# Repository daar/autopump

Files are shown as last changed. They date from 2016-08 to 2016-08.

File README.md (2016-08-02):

Autopump is a small project to create an Arduino powered automatic compressed air controller. The controller has an LCD screen and two button interface. Two automatic valves and a pressure transmitter make it possible to achieve accurate control on the target pressure. The original purpose to build such a controller was to make it possible to automatically pump soccer balls, although the controller of course can be used for any purpose.

Below is a rendering of the Arduino UNO shield that is needed to control autopump. The shield connects all peripherals to the Arduino board.

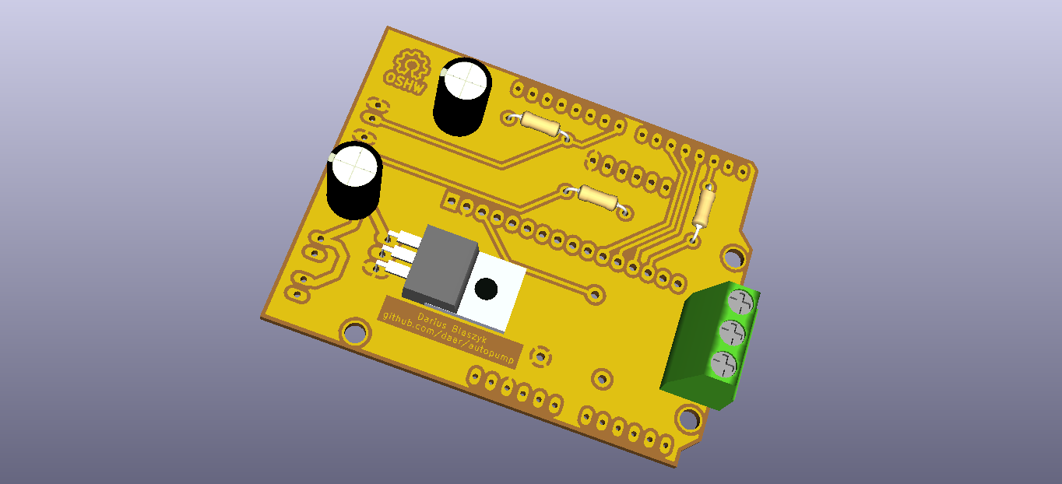
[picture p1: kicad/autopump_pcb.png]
Autopump shield: PCB rendering from KiCad


All sourcecode is released under GPL2 license and the hardware is released under the OSHW.

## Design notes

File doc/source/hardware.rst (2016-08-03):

Hardware
========
Based upon the design two air valves are needed. One to control the compressed air and one to deflate when needed. 

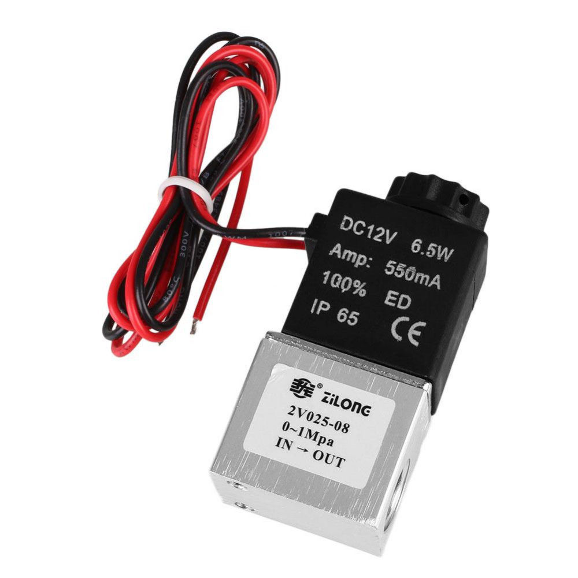
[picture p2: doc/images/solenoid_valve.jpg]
  
  
The valves are normally closed and need 12V to be opened. The Arduino UNO is not capable of controlling 12V @6.5W directly, to be able to acomplish this one needs a relay. A relay is an electrically controlled mechanic switch. This means that with a 5V pin from the Arduino you can switch a larger voltage. The relay was purchased via `MiniInTheBox.com`_.

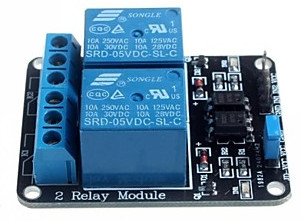
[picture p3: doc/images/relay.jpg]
  

The first relay purchased did not have optocouplers. These components transfer the electrical signals coming from the Arduino to another isolated circuit by using light. Optocouplers prevent high voltages from affecting the system receiving the signal. In the first setup, repeated switching of the relay would mess up the LCD screen caused by a voltage drop. The result was an unreadable LCD that could not be reset unless a complete reboot of the system was performed.

The next item to be bought was a pressure transducer (PT). A PT is a device that converts pressures (in this case 0 to 100PSI) to an electrical signal (0.5 to 4.5V for this item). 

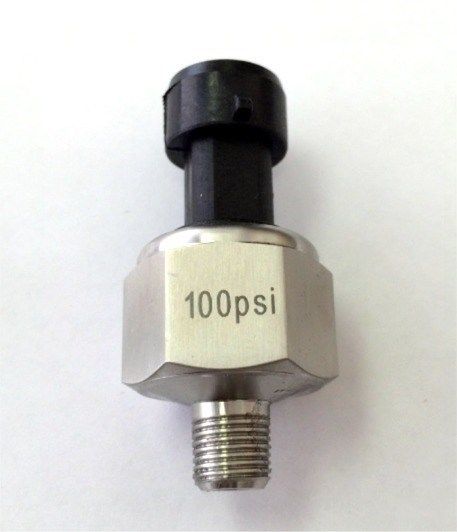
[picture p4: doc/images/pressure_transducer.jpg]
  

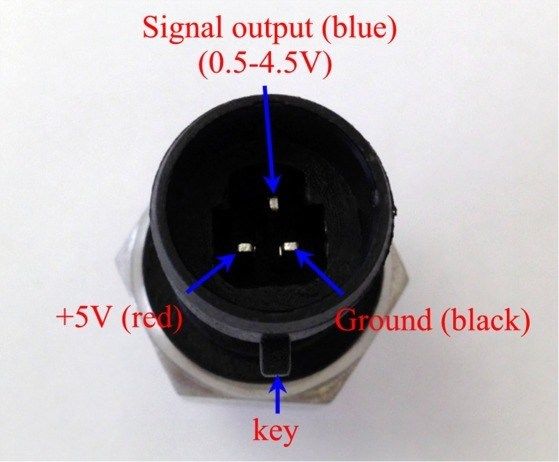
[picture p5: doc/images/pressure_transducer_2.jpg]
  

The electrical signal can be read by the Arduino UNO directly as it is between 0 to 5V. When reading the analog input the Arduino will return a value ranging from 0 to 1023 that represents the voltage of 0 to 5 V. This all needs to be taken into consideration and a regression line was formed to go directly from analog input to the actual pressure. See the graph below.

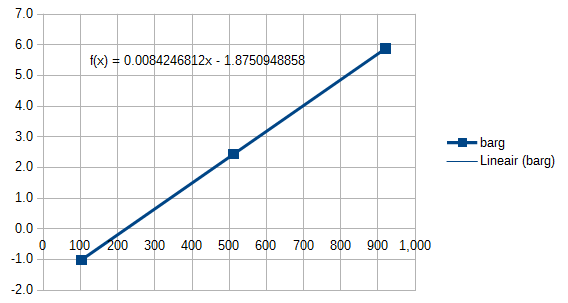
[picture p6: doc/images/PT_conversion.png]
  

On the x-axis one finds the analog value read in by the Arduino AD (analog to digital) converter and on the y-axis the actual pressure is shown.

.. _MiniInTheBox.com: http://www.miniinthebox.com

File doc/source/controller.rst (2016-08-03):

Controller
==========

The most important part of the project is the controller. For pragmatic reasons a simple to program controller was needed that is cheap and widely availabe as well. It soon appeared that an `Arduino UNO`_ is very suitable for the task. 

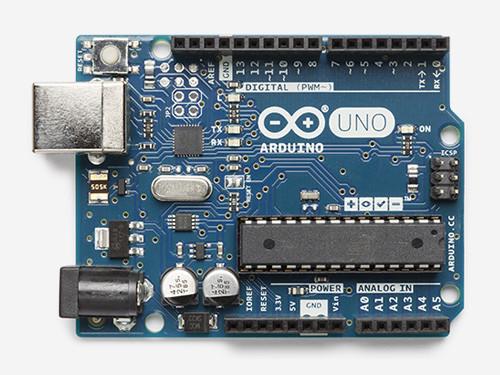
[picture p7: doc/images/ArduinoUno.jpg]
  
  
The Arduino Uno is an 8-bit microcontroller board based on the ATmega328P. It has 14 digital input/output pins (of which 6 can be used as PWM outputs) and 6 analog inputs. It basically contains everything needed to support the microcontroller; simply connect it to a computer with a USB cable or power it with a AC-to-DC adapter or battery to get started. The Arduino is programmed via the Arduino IDE in C. 

Getting started in programming the Arduino is very straightforward and intuitive. Basically the Arduino project consists of two void functions called *setup* and *loop* conveniently.

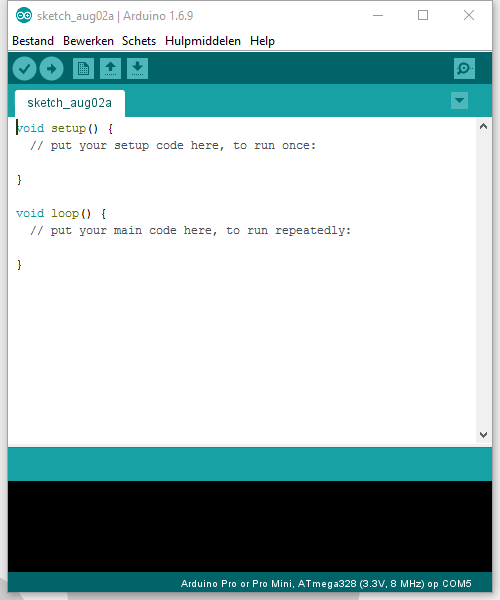
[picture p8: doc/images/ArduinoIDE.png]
  

The nice thing about the Arduino is that is has a big community and a large number of libraries and hardware supported. You can litterally find anything if you put some time and effort into it.

Officially the Arduino UNO costs about 20EUR excl. VAT, this is a low price for what you get and at the same time you support the Arduino community. I must also note that, because of the open hardware, there are also quite some cheaper alternatives. Sites like `MiniInTheBox.com`_ and `dx.com`_ sell Arduino UNO clones for around 7EUR incl. VAT.
  
Additionally two press buttons were purchased as well as a 2x16 LCD. 2x16 stands for two lines with 16 characters. Although small, it is actually more than enough for this purpose. There is really a abundance of information to be found on the internet how to program this LCD and it is actually surprisingly simple to do so. The nice thing about Arduino is that the libraries are available out of the box. No need to search and install special libraries.
  
.. _Arduino UNO: https://www.arduino.cc/en/Main/ArduinoBoardUno
.. _MiniInTheBox.com: http://www.miniinthebox.com
.. _dx.com: http://dx.com

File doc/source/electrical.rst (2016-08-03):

Electrical system
=================
The electrical system is also kept as simple as possible. First a proof of concept was made by using a breadboard to connect all the elements and test the software. A breadboard is very easy to use as it comes with a number of wires that can be used to connect electronic components to the Arduino.

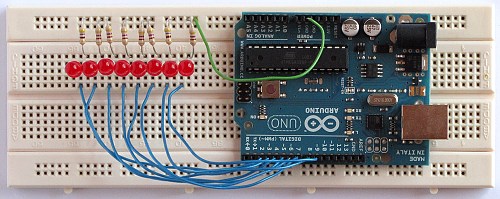
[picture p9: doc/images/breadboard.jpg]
  

Once the schematic is determined and tested, it is time to create a printed circuit board (PCB). To do this, there are a number of possibilities and software available. I have used `Fritzing`_, but unfortunately this software was a bit unstable on my computer. Fritzing is very nice to use IDE (integrated development environment). It has a lot of built in functionality and you can actually rebuild your breadboard in it, while it will convert it to a schematic for you. Another nice feature of Fritzing is that you can order your PCB right from the software.

For this project I have used `KiCAD`_ instead. KiCAD is a lot more difficult to use than Fritzing, however it's also more powerfull and versatile.

KiCAD
-----
KiCad is an open-source software tool for the creation of electronic schematic diagrams and PCB artwork. The learning curve for KiCAD is a bit steep at first but once you get a hang of it, it actually works pretty effectively. The strange thing about KiCAD is that it is a suite built up around a number of stand alone tools. This means that you need to switch quite a lot between applications (unlike Fritzing) and that you need to manually create temporary files to go from one application to the other. This is somewhat annoying, but you get used to it.
The first step you need to take in KiCAD is to create a new project and start working on the schematics. You can take the notes you made when working on the breadboard or, like I did, take the breadboard apart again one wire at a time and document that in the schematics editor of KiCAD.

.. _Fritzing: http://fritzing.org
.. _KiCAD: http://kicad-pcb.org

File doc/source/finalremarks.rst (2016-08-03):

Final remarks
=============

Creating autopump was most of all a fun excersise. I really hope other people will follow and create their own autopump. It's easy, fun and not too expensive to make one. If you create one of your own, I would really appreciate if you could send me a line via `email`_ including a picture of the result so I can post it up here.

Cost
----
The cost of the autopump is kept as low as possible so it will be feasible for others to create one by themselves. Of course there is a basic amount of hardware you need, including the Arduino, but as explained there are a number of resources where you can get it relatively cheap from even without posting costs in some cases! I will try to make a comprehensive list of all parts used below. I case I forgot something you can `email`_ me and I will correct it here.

   +-----------------------+-----------------------+-----------------------+
   | Item                  | Price                 | Site                  |
   +=======================+=======================+=======================+
   | Arduino UNO           |                       |                       |
   +-----------------------+-----------------------+-----------------------+
   | 2 chanel relay        |                       |                       |
   +-----------------------+-----------------------+-----------------------+
   | Air solenoid valves   |                       |                       |
   +-----------------------+-----------------------+-----------------------+
   | Pressure transducer   |                       |                       |
   +-----------------------+-----------------------+-----------------------+
   | Enclosure             |                       |                       |
   +-----------------------+-----------------------+-----------------------+
   | Air tubing            |                       |                       |
   +-----------------------+-----------------------+-----------------------+
   | PCB board             |                       |                       |
   +-----------------------+-----------------------+-----------------------+
   | Electronic components |                       |                       |
   +-----------------------+-----------------------+-----------------------+

.. _email: dhkblaszyk@gmail.com

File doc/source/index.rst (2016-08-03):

.. Autopump documentation master file, created by
   sphinx-quickstart on Tue Aug  2 13:29:18 2016.
   You can adapt this file completely to your liking, but it should at least
   contain the root `toctree` directive.

Welcome to Autopump's documentation!
====================================

Contents:

.. toctree::
   :maxdepth: 1

   getting_started
   controller
   hardware
   software
   electrical
   construction
   operation
   finalremarks

Autopump is a small project to create an Arduino powered automatic compressed air controller. The controller has an LCD screen and two button interface. Two automatic valves and a pressure transmitter make it possible to achieve accurate control on the target pressure. The original purpose to build such a controller was to make it possible to automatically pump soccer balls, although the controller of course can be used for any purpose.

All sourcecode is released under GPL2 license and the hardware is released under the OSHW.

This document describes all the steps that needed to be taken to finish this project. Different skills are needed (software, hardware and electronics) to be able to complete this project. I have tried to make a comprehensive desicription, however, if you find details are missing, you can contact me via `email`_ with your questions. I hope people get inspired by this project as I did and try and persevere to fabricate their own projects.

.. _email: dhkblaszyk@gmail.com
   
Indices and tables
==================

* :ref:`genindex`
* :ref:`modindex`
* :ref:`search`

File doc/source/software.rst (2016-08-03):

Software
========

The software is kept as simple as possible. In principle there are four modes in which the software can be in. The next diagram displays how it works.

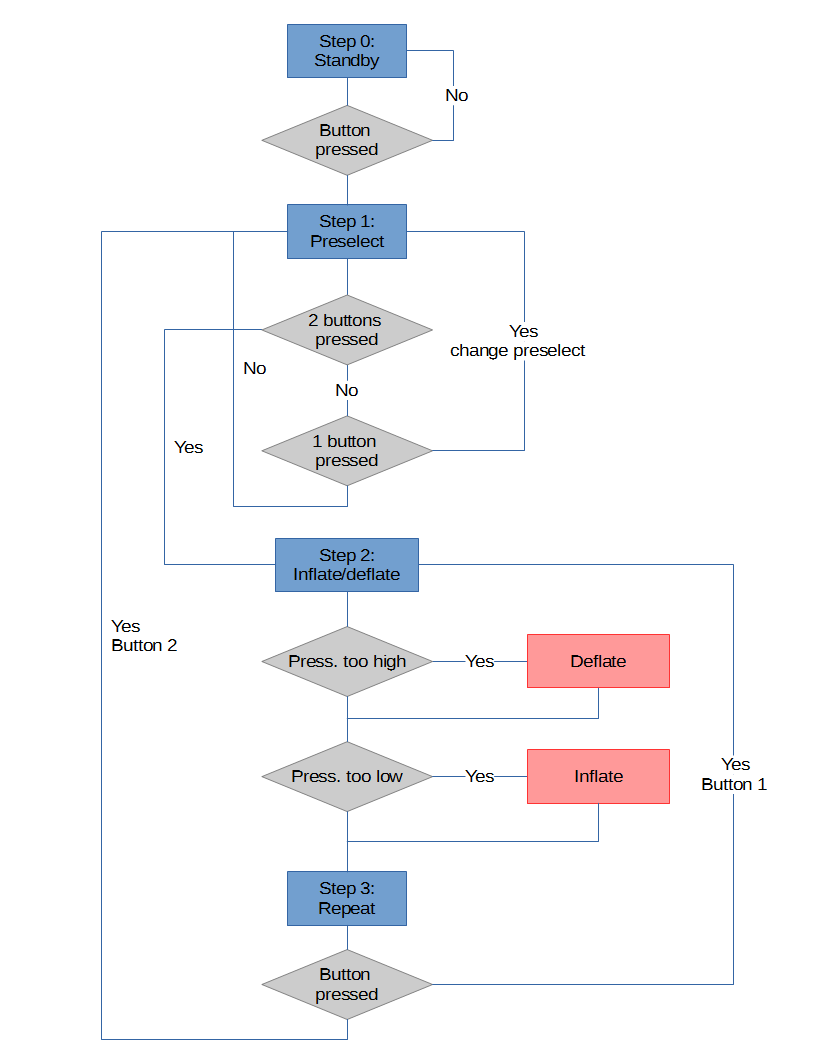
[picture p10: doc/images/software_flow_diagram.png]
  

Step 0
------
When in step 0, the system is in standby. This means that the LCD screen is turned of to indicate standby (save some power and lifetime of the LCD). Meanwhile the actual pressure of the system is read and stored as *zeropressure*. This *zeropressure* variable is actually the actual outside pressure. When inflating, the target pressure is set relative to the outside pressure. So therefore the *zeropressure* is determined to compensate for it. At the same time the state of the press buttons are determined. If one of the buttons is pressed then the system will activate the LCD screen and go to step 1.

Step 1
------
Once the software is in step 1, the user can switch pre-selects. There are a number of them hardcoded in the software. Any button push will increase the preselect index, until the maximum is reached and the index is reset to 0. A push of both buttons at the same time will trigger the software to go to step 2. There is also a timer started in this step that will put the system to standby after 1 minute being idle.

Step 2
------
The object to be inflated is expected to be already connected to the device in step 1. The software will now check if the objects needs to be deflated, if so it will open the correct valve. Once done a similar check for inflation is performed. This deflate / inflate cycle is repeated once just to be sure. In between the inflate and deflate steps there is a one second delay to stabilize the pressure measurement. Also in this step there is an idle timer of one minute started.

Step 3
------
Once done, the software progresses to step 3, where the user can decide to either re-run using the same parameters, but possibly a different object, or to select a new target pressure and goto step 1. If the system remains idle for one minute it will return to step 0.

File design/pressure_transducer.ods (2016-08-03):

PSI | V | analogRead | bar | barg
0 | 0.5 | 102 | 0.000 | -1.013 | 0.000
50 | 2.5 | 512 | 3.447 | 2.434 | 2.614
100 | 4.5 | 921 | 6.895 | 5.882 | 5.228
20 | 1.3 | 266 | 1.379 | 0.366 | 1.046 | ← use this line for testing
 |  |  |  |  |  | ← calculates regression line for analogRead to pressure in barg

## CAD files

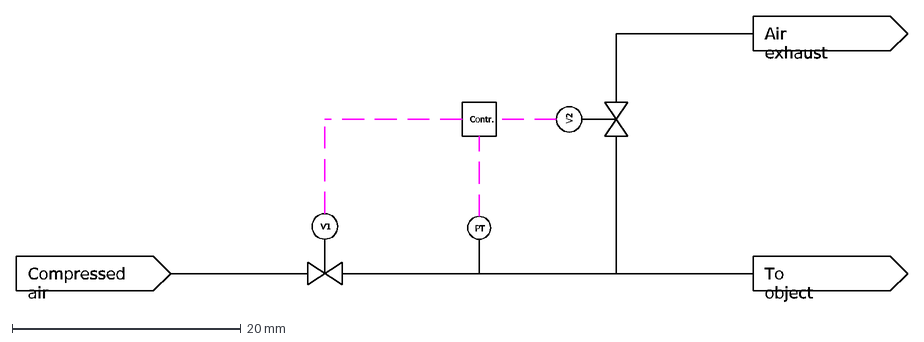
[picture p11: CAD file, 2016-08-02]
design/design.dxf
Compressed air
V1
PT
Contr.
Air exhaust
To object
V2

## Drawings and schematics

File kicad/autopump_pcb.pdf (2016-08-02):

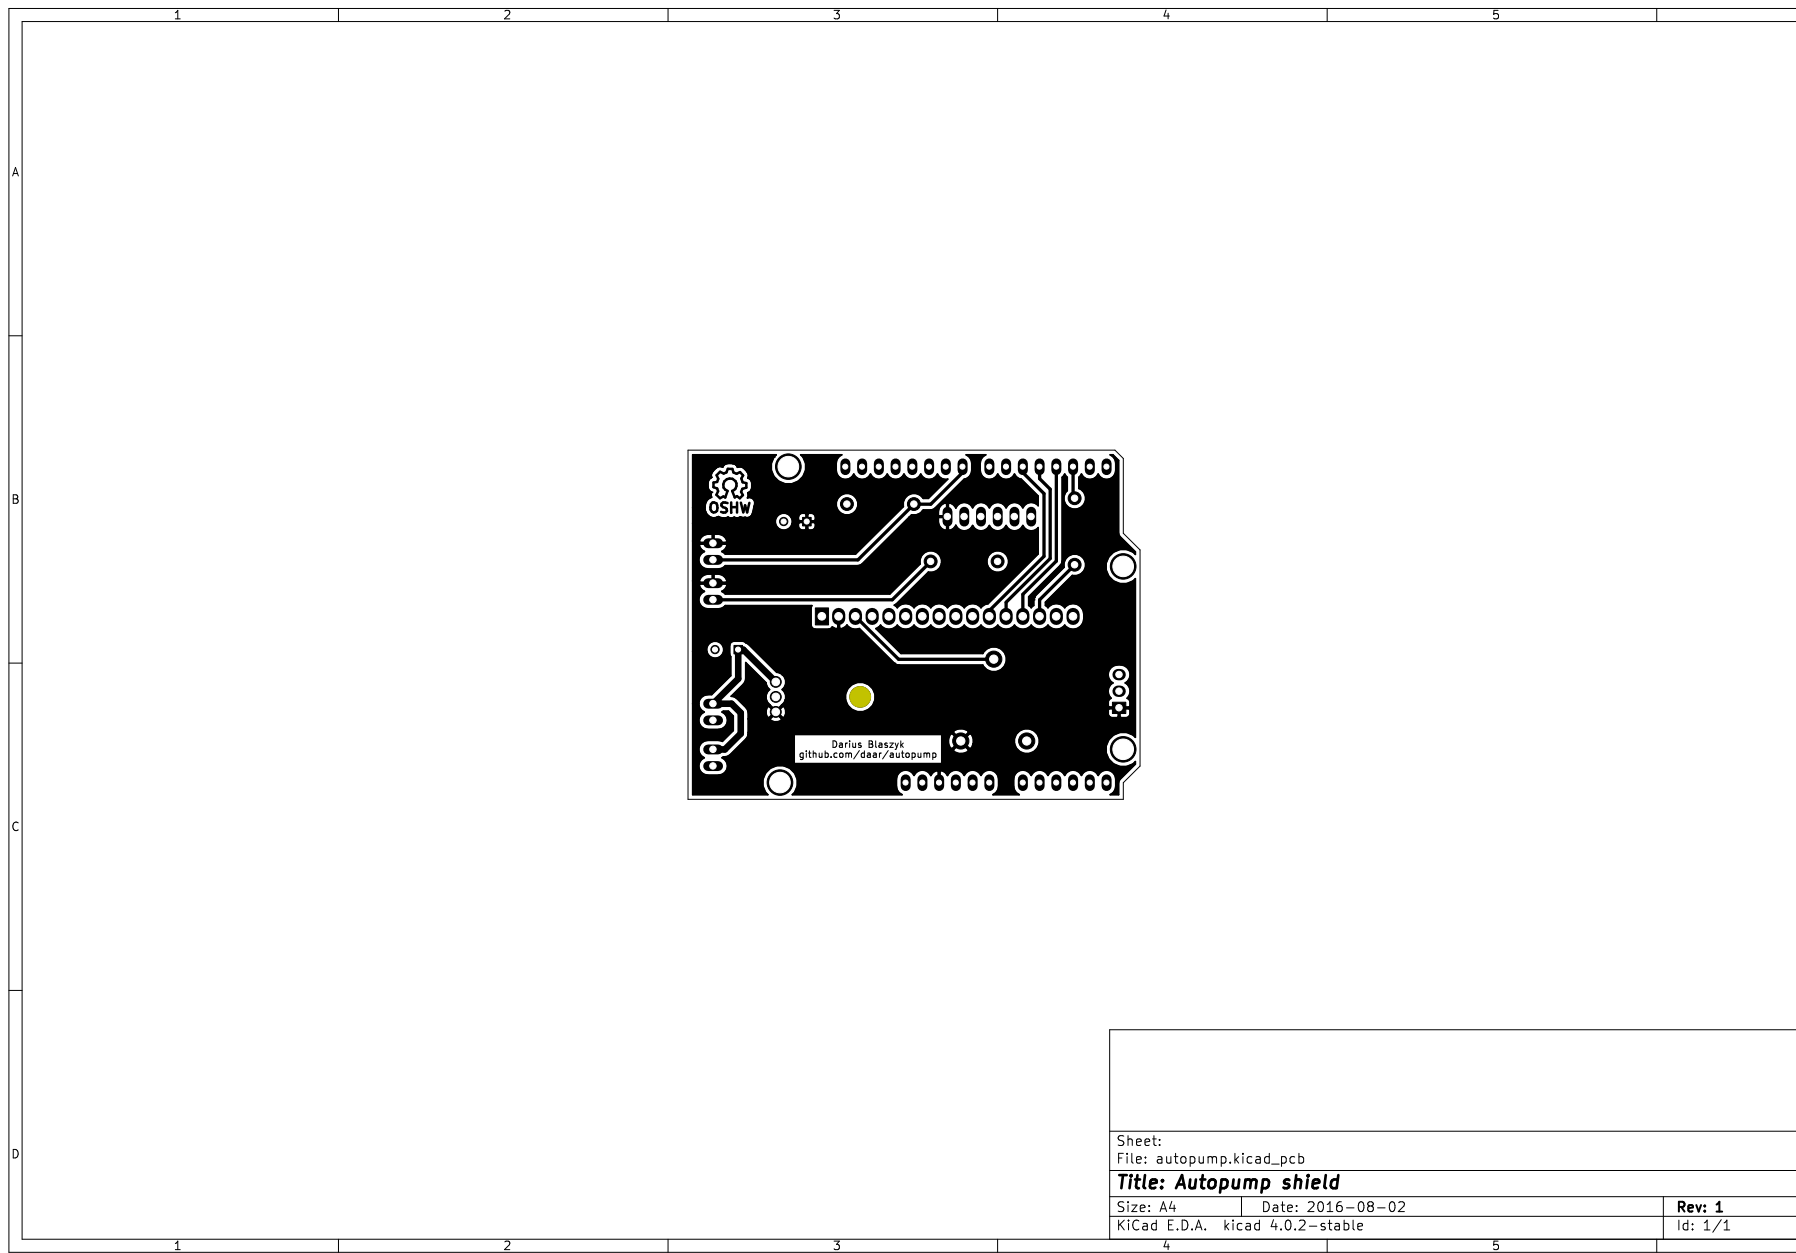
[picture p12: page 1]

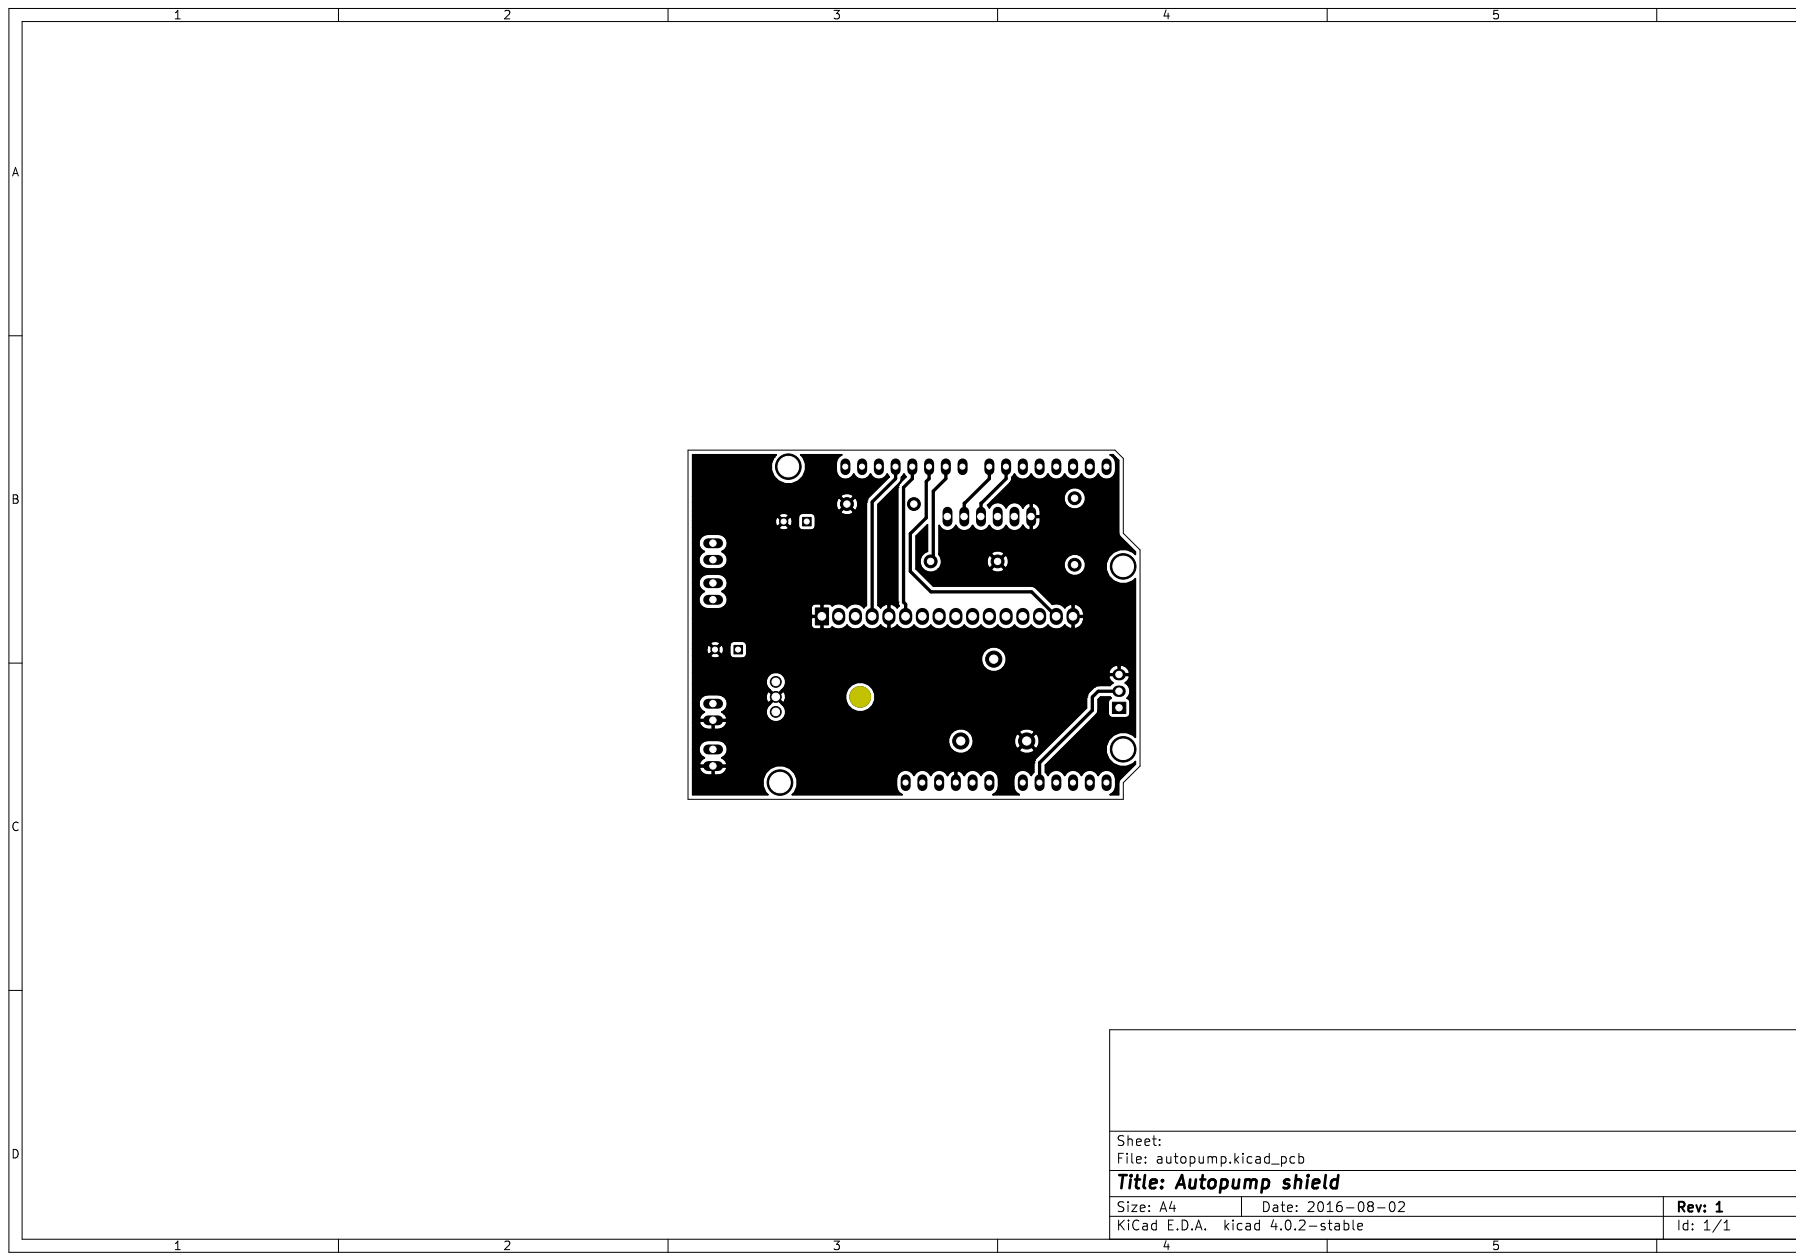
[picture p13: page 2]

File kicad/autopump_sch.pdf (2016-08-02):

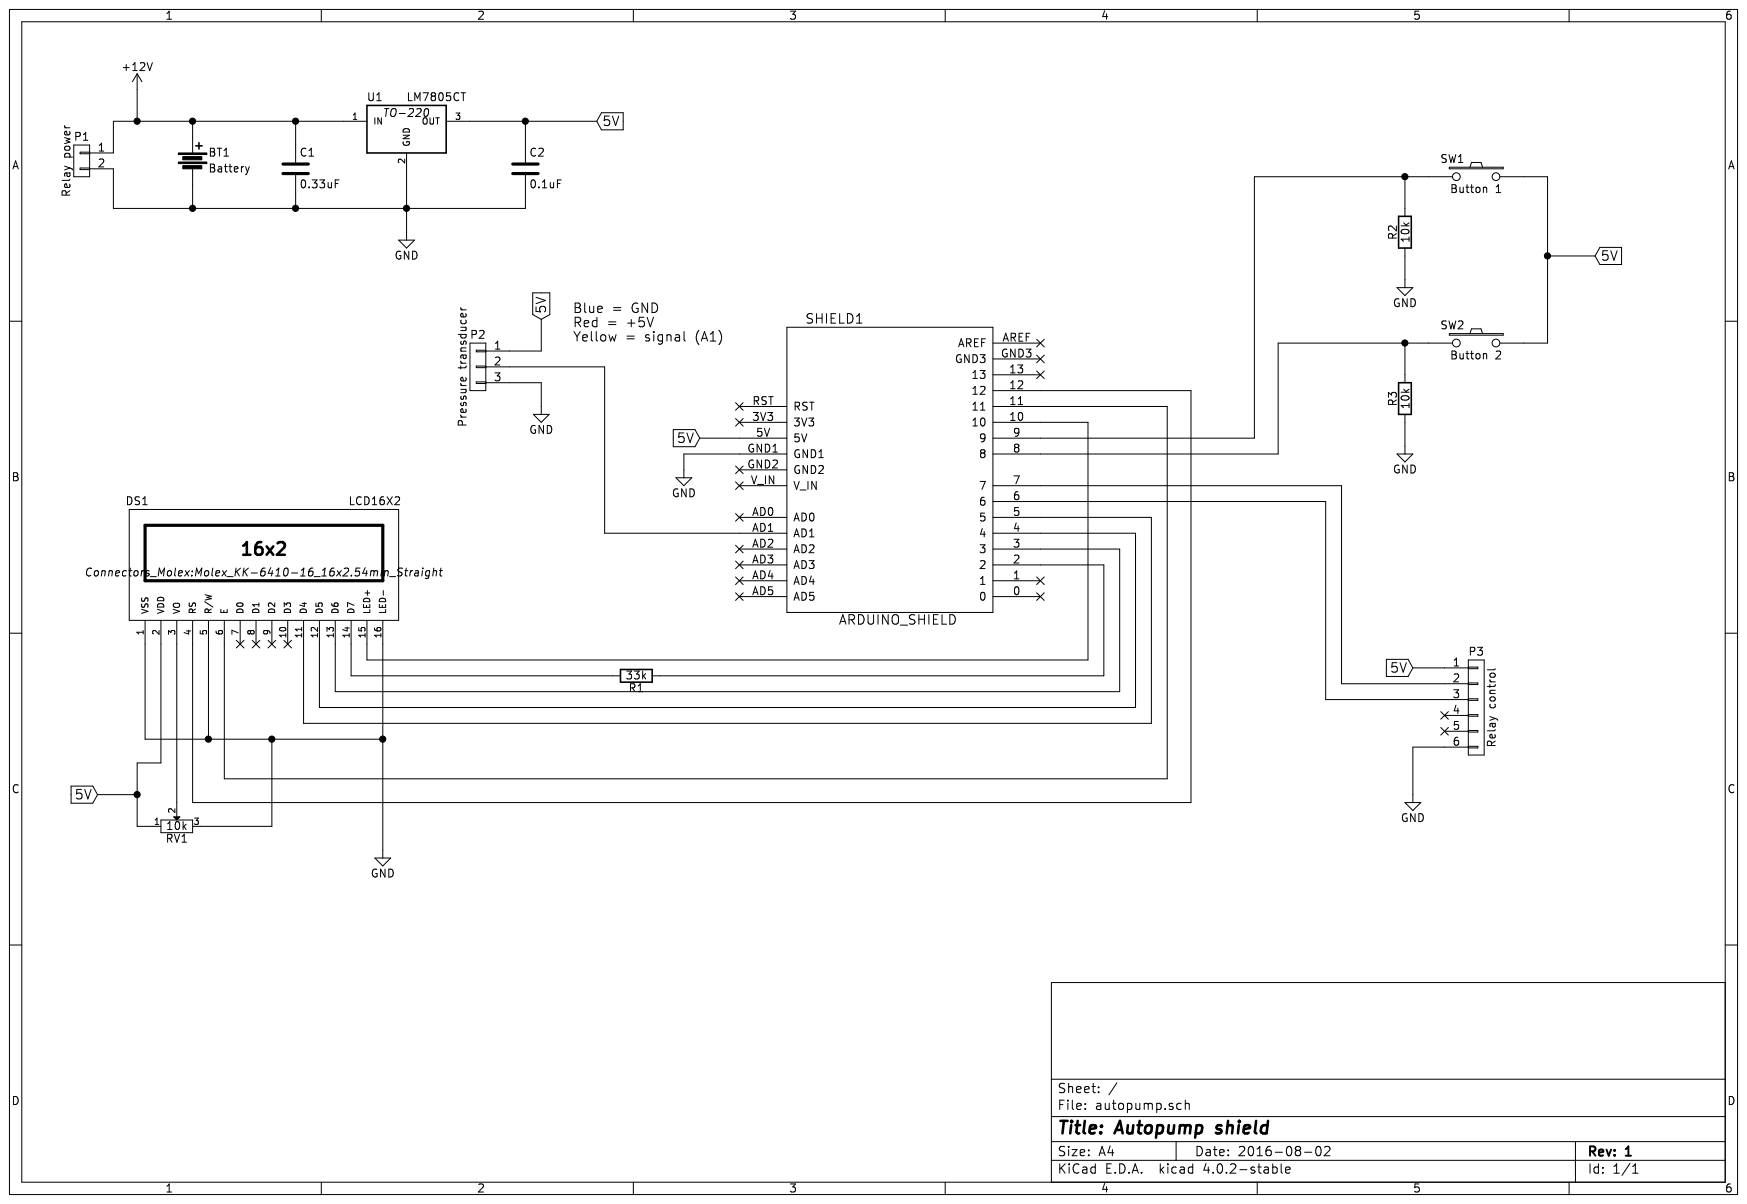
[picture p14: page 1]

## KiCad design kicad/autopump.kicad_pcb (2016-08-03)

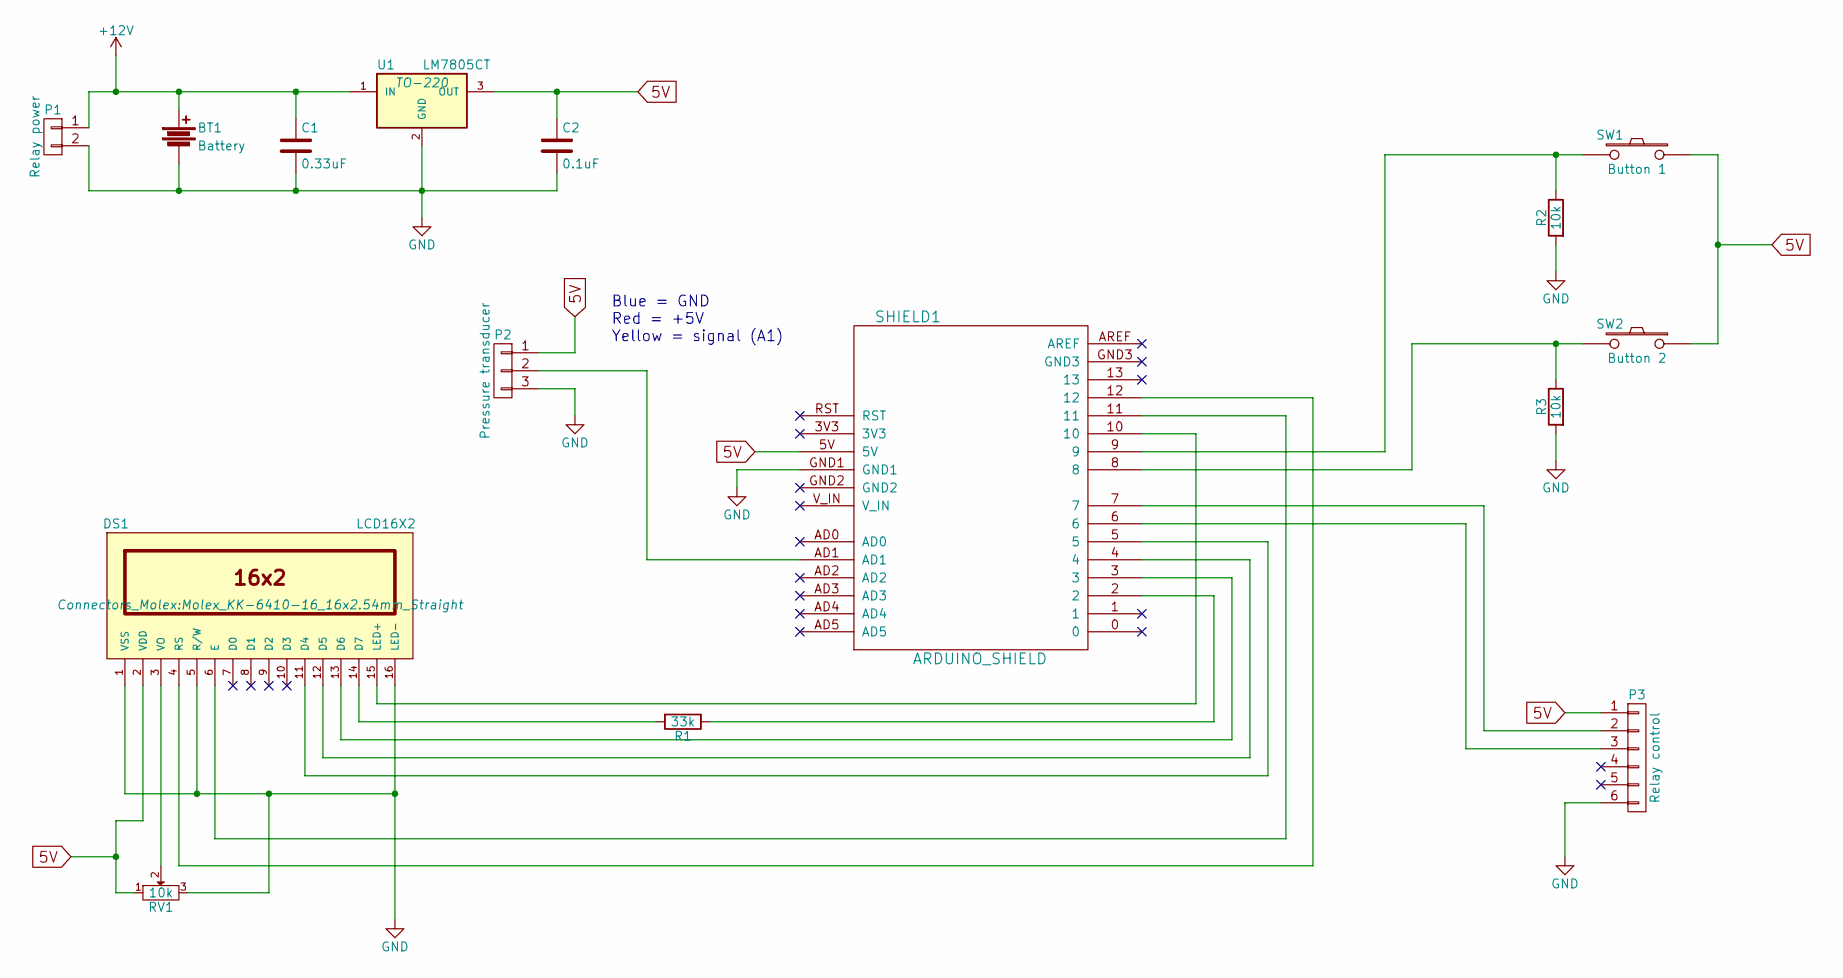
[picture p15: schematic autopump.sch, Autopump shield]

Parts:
BT1: Battery; PINHEAD1-2
C1: 0.33uF; C_Radial_D8_L11.5_P3.5
C2: 0.1uF; C_Radial_D8_L11.5_P3.5
DS1: LCD16X2; Molex_KK-6410-16_16x2.54mm_Straight
P1: Relay power; PINHEAD1-2
P2: Pressure transducer; Socket_Strip_Straight_1x03
P3: Relay control; PINHEAD1-6
R1: 33k; Resistor_Horizontal_RM10mm
R2, R3: 10k; Resistor_Horizontal_RM10mm
RV1: 10k; Potentiometer_Trimmer-Piher_PT15-V12-5_horizontal
SHIELD1: ARDUINO_SHIELD; ARDUINO SHIELD
SW1: Button 1; PINHEAD1-2
SW2: Button 2; PINHEAD1-2
U1: LM7805CT; TO-220

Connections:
5V: C2.1, DS1.2 (VDD), P2.1, P3.1, RV1.1, SHIELD1.5V, SW1.1, SW2.1, U1.3 (OUT)
+12V: BT1.1, C1.1, P1.1, U1.1 (IN)
GND: BT1.2, C1.2, C2.2, DS1.1 (VSS), DS1.5 (R/W), DS1.16 (LED-), P1.2, P2.3, P3.6, R2.2, R3.2, RV1.3, SHIELD1.GND1, U1.2 (GND)
unnamed: DS1.3 (VO), RV1.2
unnamed: DS1.4 (RS), SHIELD1.12
unnamed: DS1.6 (E), SHIELD1.11
unnamed: DS1.11 (D4), SHIELD1.5
unnamed: DS1.12 (D5), SHIELD1.4
unnamed: DS1.13 (D6), SHIELD1.3
unnamed: DS1.14 (D7), R1.2
unnamed: DS1.15 (LED+), SHIELD1.10
unnamed: P2.2, SHIELD1.AD1
unnamed: P3.2, SHIELD1.7
unnamed: P3.3, SHIELD1.6
unnamed: R1.1, SHIELD1.2
unnamed: R2.1, SHIELD1.9, SW1.2
unnamed: R3.1, SHIELD1.8, SW2.2

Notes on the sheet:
Blue = GND Red = +5V Yellow = signal (A1)

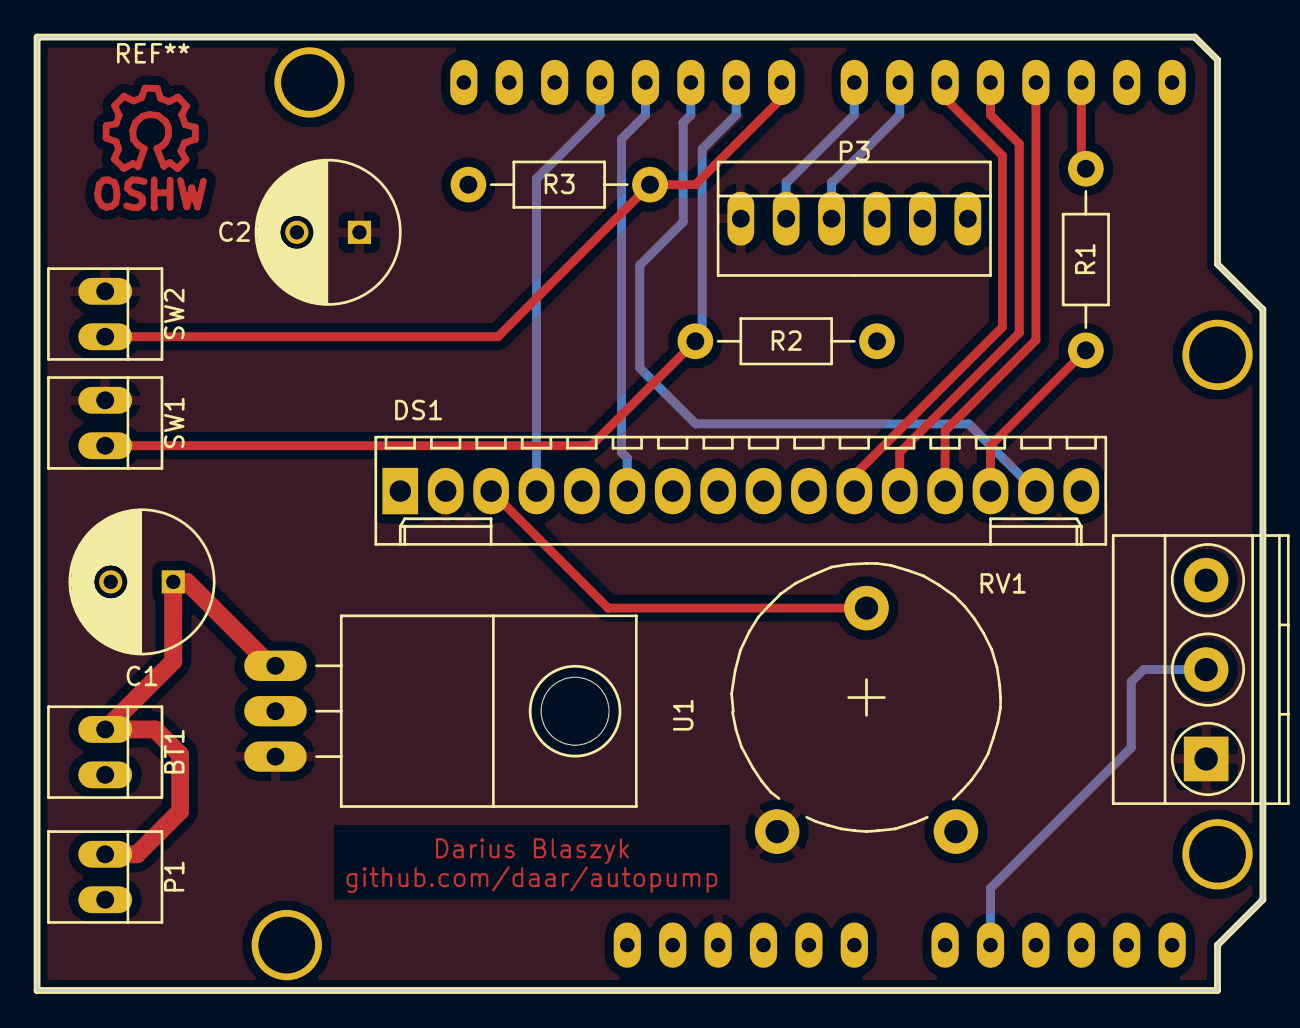
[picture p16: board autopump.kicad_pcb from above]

Board: 2 copper layers, 68.6 x 53.3 mm, 15 parts (0 on the bottom side), 17 nets.

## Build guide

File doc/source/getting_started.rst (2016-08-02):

Getting started
===============
The initial reason to start such a project was to create an automatic ball pump. This project was born out of frustration and lack of a commercial alternative. The first step that needed to be taken was to make a design. Based on this design all hardware will be purchased and then the software will be written. Below is the P&ID (piping and instrumentation diagram) that was made for this project.

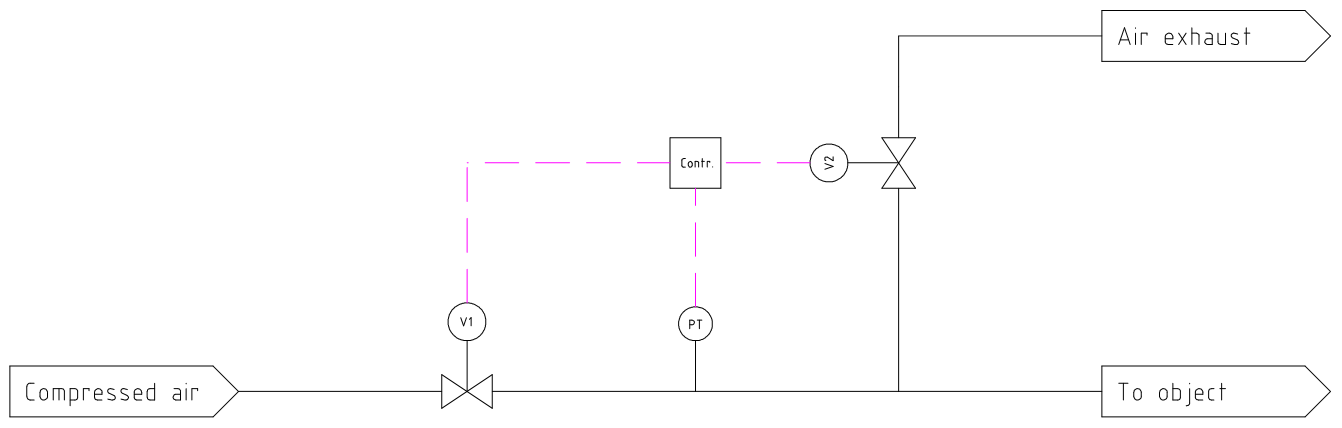
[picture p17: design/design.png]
  
  
The diagram shows that two air valves (V1 & V2) will control if the object is inflated or deflated. A pressure sensor (PT) will measure the actual pressure and depending on the measured value either of the valves is opened until the desired pressure is reached.

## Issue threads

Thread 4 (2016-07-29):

fix the assignment of track widths for 12V lines

daar, 2016-07-29:

daar, 2016-08-02:
fixed in revision 18

Closed 2016-08-02.

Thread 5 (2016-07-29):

Review the connections on the board

daar, 2016-07-29:
If possible all connections to external parts and boards should be on the edge of the PCB. On either end a detachable connection should be foreseen.

P2 - pressure transducer (3pin)
DS1 - LCD

daar, 2016-08-02:
fixed in revision 18

Closed 2016-08-02.

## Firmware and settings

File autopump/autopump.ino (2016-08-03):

/*
  Copyright (C) 2015-2016  Darius Blaszyk

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
  You should have received a copy of the GNU General Public License
  along with this program; if not, write to the Free Software
  Foundation, Inc., 51 Franklin Street, Fifth Floor, Boston, MA  02110-1301, USA.
*/

// include the library code:
#include <LiquidCrystal.h>

#define DISPLAYTIME 500                 //refresh rate in ms for the display

#define PRESSURE_INPUT 1                //analog input of the pressure transducer

#define BUTTON_1 8                      //pin of pushbutton 1
#define BUTTON_2 9                      //pin of pushbutton 2

#define VALVE_1 6                       //pin of valve 1
#define VALVE_2 7                       //pin of valve 2

#define BACKLIGHT 10                    //pin of backlight control

#define PRESELECTMAX 3                  //number of presets

#define RESETTIME 60000                 //time to goto standby in ms
#define DEFLATETIME 10000               //max time needed for deflation in ms
#define INFLATETIME 10000               //max time needed for inflation in ms

int stepnr = 0;

double zeropressure = 0;
double pressure = 0;
double pressuretol = 0.01;              //tolerance of pressure

unsigned long stime = 0;                //step timer
unsigned long dtime = 0;                //display timer

int preselectnr = 0;
double preselectpressure = 0;
double preselectval[PRESELECTMAX] = {
  0.8, 0.9, 1.0
};
char* preselectstr[] = {
  "Pupillen", "Junioren", "Senioren"
};

// initialize the library with the numbers of the interface pins
LiquidCrystal lcd(12, 11, 5, 4, 3, 2);

void setup() {
  Serial.begin(9600);

  //pushbutton 1 and 2
  pinMode(BUTTON_1, INPUT);
  pinMode(BUTTON_2, INPUT);

  //backlight control pin
  pinMode(BACKLIGHT, OUTPUT);

  //valve 1 and 2
  pinMode(VALVE_1, OUTPUT);
  pinMode(VALVE_2, OUTPUT);

  //close deflate valve
  digitalWrite(VALVE_1, LOW);

  //close inflate valve
  digitalWrite(VALVE_2, LOW);

  // set up the LCD's number of columns and rows:
  lcd.begin(16, 2);
  lcd.display();
}

/*
 * This function converts the analog signal of the pressure transducer
 * to a pressure. The unit is in bar(g).
 */
void readpressure() {
  int raw_pressure = analogRead(PRESSURE_INPUT);
  pressure = 0.006388082 * raw_pressure - 0.653500811;
  
  Serial.print(zeropressure, DEC);
  Serial.print(" ");
  Serial.println(pressure, DEC);
}

void printdisplay() {

  char line1[16];
  char line2[16];
  char temp[16];

  if (millis() - dtime < DISPLAYTIME) {
    return;
  }

  dtime = millis();

  lcd.clear();

  switch (stepnr) {

    case 0:
      {
        //standby, no display
        digitalWrite(BACKLIGHT, LOW);
        lcd.noDisplay();
      }
      break;

    case 1:
      {
        //display preset
        digitalWrite(BACKLIGHT, HIGH);
        lcd.display();
        
        dtostrf(preselectpressure, 5, 3, temp);
        sprintf(line2, "target: %sBar", temp);

        lcd.print("preset: ");
        lcd.print(preselectstr[preselectnr]);

        //lcd.print(line1);
        lcd.setCursor(0, 1);
        lcd.print(line2);
      }
      break;

    case 2:
      {
        digitalWrite(BACKLIGHT, HIGH);
        lcd.display();
        
        double corrpressure = pressure - zeropressure;
        //print the actual pressure
        if (corrpressure < 0) {
          lcd.print("actual:");
        } else {
          lcd.print("actual: ");
        }
        dtostrf(corrpressure, 5, 3, temp);

        lcd.print(temp);
        lcd.print("Bar");

        //print the target pressure
        dtostrf(preselectval[preselectnr], 5, 3, temp);
        sprintf(line2, "target: %sBar", temp);

        //lcd.print(line1);
        lcd.setCursor(0, 1);
        lcd.print(line2);
      }
      break;

    case 3:
      {
        digitalWrite(BACKLIGHT, HIGH);
        lcd.display();
        
        //waiting for restart or reset
        lcd.print("Btn 1 for repeat");
        lcd.setCursor(0, 1);
        lcd.print("Btn 2 for reset");
      }
      break;
  }
}

void deflate() {

  stime = millis();
  while (pressure - zeropressure > preselectpressure + pressuretol && millis() - stime < DEFLATETIME ) {

    digitalWrite(VALVE_1, HIGH);
    readpressure();

    printdisplay();
  }
  digitalWrite(VALVE_1, LOW);
}

void inflate() {

  stime = millis();
  while (pressure - zeropressure < preselectpressure - pressuretol && millis() - stime < INFLATETIME) {

    digitalWrite(VALVE_2, HIGH);
    readpressure();

    printdisplay();
  }
  digitalWrite(VALVE_2, LOW);
}

void loop() {
  Serial.print(stepnr);
  Serial.print(' ');

  //read button 1 state
  int button1 = digitalRead(BUTTON_1);
  Serial.print(button1, DEC);

  //read button 2 state
  int button2 = digitalRead(BUTTON_2);
  Serial.print(button2, DEC);

  Serial.print(' ');

  //read pressure
  readpressure();

  //determine preselect pressure
  preselectpressure = preselectval[preselectnr];

  switch (stepnr) {

    //standby
    case 0:
      {
        //store zero pressure
        zeropressure = pressure;

        if (button1 || button2) {
          stepnr = 1;

          //allow the buttons to be unpressed, otherwise we already select
          //the next preset
          delay(1000);
          
          stime = millis();
        }

        printdisplay();
      }
      break;

    //pre-select set pressure
    case 1:
      {
        //one button pressed means change preselect
        if (button1 || button2) {

          //allow both buttons to be pressed
          delay(1000);

          //recheck buttons
          button1 = digitalRead(BUTTON_1);
          button2 = digitalRead(BUTTON_2);

          //if both buttons pressed then start
          if (button1 && button2) {
            stepnr = 2;
          } else
          {

            preselectnr = preselectnr + 1;
            if (preselectnr >= PRESELECTMAX) {
              preselectnr = 0;
            }
          }
          stime = millis();
        }

        printdisplay();

        //after resettime has elapsed goto standby
        if (millis() - stime >= RESETTIME) {

          stepnr = 0;
        }
      }
      break;

    //start adjusting pressure
    case 2:
      {

        //run the deflate and inflate cycles two times each
        //in between cycles pause 1sec to stabilize the measurement

        delay(1000);
        deflate();
        delay(1000);
        inflate();
        delay(1000);
        deflate();
        delay(1000);
        inflate();


        stepnr = 3;
        stime = millis();
      }
      break;

    //wait for restart or reset
    case 3:
      {
        printdisplay();

        //if button 1 pressed than restart the same sequence
        if (button1) {
          stepnr = 2;
          stime = millis();
        }
        else if (button2) {
          stepnr = 1;
          stime = millis();
        }

        //after resettime has elapsed goto standby
        Serial.println(millis() - stime);
        Serial.println(RESETTIME);
        if (millis() - stime >= RESETTIME) {

          stepnr = 0;
        }
      }
      break;
  }
}

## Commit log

2016-07-16 More work on the autopump source code. The basic code is now implemented. Please note that TFT screen support has been droped in favor of LCD screen support. A start has been made with creating a fri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
    [autopump.fzz]
2016-07-17 autopump - added one more preset - reorganized some variables and code - turn of LCD display in step 0 - automatic formatting of source code - added automatic reset time to steps 1 and 2 - renamed ti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
    parts
    - added pictures and description of some of the parts used
    [autopump.ino]
2016-07-20 fixed quite some issues while debugging; - damping LCD screen output - fixing output (first line) - fixed changing steps form 1 -> 2 - added some more debugging to serial monitor - and some more
    [autopump.ino]
2016-07-21 run the deflate and inflate cycles two times consecutively for optimal results display update is controlled in printdisplay() changed order of presets from small to large
2016-07-21 define calculations are written out full, somehow this did not work properly giving false results pressure tolerance from 0.05bar to 0.01bar (just a guess now) increased the preselect values a little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
    [autopump.ino]
2016-07-25 Removed the fritzing files. Unfortunatly fritizing does not seem to be stable here. Initial work using kicad. Please note that the work is far from ready. Need to add a few items like: - transistor t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
    [autopump.dsn, autopump.fzz, autopump.kicad_pcb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]
2016-07-27 More work on the PCB. - make use of the and Arduino shield (http://www.thingiverse.com/thing:9630) library. - reorganize layouts of components - changed the track width and clearances a bit wider - a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
    [autopump.dsn, autopump.kicad_pcb, autopump.sch]
2016-07-28 More work on the schema and PCB - fixed and reorganized the power supply in the schema - changed the footprints to be more suitable - reorgnized the footprints slightly on the PCB for better layout a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
    [autopump.dsn, autopump.kicad_pcb, autopump.sch]
2016-08-02 Removed some unneeded kicad files from github Replaced LM7805 component by the LM7805CT component Added +12V symbol to schema so the PCB design rules work again. Issue #4 Reorganized the board a bit 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
    [autopump.dsn, autopump.kicad_pcb, autopump.sch]
2016-08-02 initial import of documentation for this project import of design files, which are also used in the documentation
    [design.dxf]
2016-08-02 Added images to the documentation Added some more text to the documentation topics hardware and controller Renamed arduino_uno.rst to controller.rst
2016-08-03 doc - added quite some more documentation (self explanatory) - added some images to illustrate the documentation kicad - moved the text a bit on the PCB for better alignment between the components de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
    [autopump.kicad_pcb, pressure_transducer.ods]
2016-08-03 src - pressure input pin is now a define - be a bit more verbose and print zeropressure to serial - add a delay of 1000ms entering step 2 - renamed the src folder to arduino as the Arduino IDE needs 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

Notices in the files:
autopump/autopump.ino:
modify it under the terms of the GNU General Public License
